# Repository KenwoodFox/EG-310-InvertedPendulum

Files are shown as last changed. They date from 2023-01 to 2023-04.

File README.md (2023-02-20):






EG-310 Inverted Pendulum
========================

This project is full of blank media! It will need filling out and cleaning before production, you have been warned!

# Welcome!

Put a welcome here!

# Getting Started

## Cloning this repo

First, clone this repo (and optionally checkout a branch)

```shell
git clone https://github.com/KenwoodFox/InvertedPendulum.git
cd InvertedPendulum
```

## Init Submodules

Some libraries and resources are included as git submodules, run the following
command to initialize them before opening the main sch

(If you get a missing library error, make sure to do this!)

```shell
git submodule update --init --recursive
```

# Where is everything?!

Look to...
```shell
├── CAD                     # CAD and design files
├── Firmware                # Software and Firmware source code
├── Hardware                # PCB And component design files
└── Media
    ├── Notes               # Notes and scratch ideas/misc resources
    ├── Letters             # Status letters, letters of request, etc
    └── Presentations       # Presentations (CDR, FDR..)
```

# I just want to edit a single file!

Start by cloning this repo down and making a new branch, offical team communication
is through discord so hop on over any time! If you're new to git check out this video: https://youtu.be/mJ-qvsxPHpY

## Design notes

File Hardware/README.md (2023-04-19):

# Hardware

All the hardware for the inverted pendulum is made with (KiCAD)[https://www.kicad.org/]!

All the automation for this project is done with (KiBot)[https://github.com/INTI-CMNB/KiBot]

## Getting Started

Always clone this repo using submodules!

```shell
git clone --recurse-submodules https://github.com/KenwoodFox/EG-310-InvertedPendulum.git
```

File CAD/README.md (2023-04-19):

# CAD

The cad is a mix of Inventor and FreeCAD.

## Directory

```
.
├── Components                                            ; FreeCAD Misc Parts
├── Cosmetic                                              ; Badges and cosmetic
├── Frame Pieces                                          ; Frame Pieces
├── Matt's CDR CAD Files (Inventor Professional Format)   ; Matt's Inventor Files
│   ├── Assemblies                                        ; Inventor Assemblies
│   │   ├── Carriage Assemblies
│   │   └── Frame Assemblies
│   ├── Components and Part Files                         ; Inventor Components and Parts
│   │   ├── Carriage Components
│   │   └── Frame Components
│   ├── Drawings                                          ; Inventor Drawings
│   │   └── Different Carriage Type Exploded Drawings
│   └── Exploded Views                                    ; Exploded Views
│       └── DIfferent Carriage Type Presentations
└── Resources                                             ; Resources stencils and templates
```

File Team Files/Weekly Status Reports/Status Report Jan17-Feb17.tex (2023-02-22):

% Formatting
\documentclass{scrartcl}
\usepackage{hyperref}
\usepackage{makeidx}
    \makeindex
\usepackage{xparse}

\usepackage{graphicx}
\graphicspath{ {.} }

\usepackage[most]{tcolorbox}
\NewDocumentCommand\newtcbtheoremautoindex{ O{} m  m m m }{%%
\newtcbtheorem[#1]{#2inner}{#3}{#4}{#5}%
\NewDocumentEnvironment { #2 } { s O{} m m }
{\IfBooleanTF{##1}
   {\begin{#2inner}[##2]{##3}{##4}}% not to index
   {\begin{#2inner}[##2, index={##3}]{##3}{##4}}% to index
} {\end{#2inner}}
% starred version (not labeled and not listed in lists of theorems):
\NewDocumentEnvironment { #2* } { O{} m }
   {\begin{#2inner*}[##1]{##2}}% (and no index as well)
   {\end{#2inner*}}
}%%

\newtcbtheoremautoindex[]{defi}{}{}{def}

% End formatting

% ====================
% Begin Status report!
% ====================

\begin{document}
\section*{EG-310 Weekly Status Report}
\begin{center}
    \begin{tabular}{ l l }
        Project Lead     & Joseph Sedutto          \\
        Date             & \today         \\
        Reporting Period & January 17 - Febuary 17
    \end{tabular}
\end{center}

\begin{defi}{Project Status Summary}{}
    \begin{tabular}{ l l r }
        Budget   & On Track & We have begun spending and qouting         \\
        Schedule & On Track & We are slightly behind schedule                     \\
        Scope    & On Track & We are within scope.
    \end{tabular}
\end{defi}

\begin{defi}{Work Completed this week}{}
    - Created inital frame and CAD \\
    - Completed inital revision of PCB \\
    - Completed PDR and presented \\
    - Reviewed PDR feedback and created inital CDR
\end{defi}

\begin{defi}{Open issues}{}
    % Check open issues https://github.com/KenwoodFox/EG-310-InvertedPendulum/issues
    No issues and \href{https://github.com/KenwoodFox/EG-310-InvertedPendulum/pulls}{four pull requests} are waiting for feedback or review.
\end{defi}

\begin{defi}{Todo for next week}{}
    % Check projects tab https://github.com/users/KenwoodFox/projects/1
    - Finalize PDP draft for submission on January 30, 2021.  \\ 
    - Convert PDP data into a simplistic slideshow format. \\
    - Create more sketches of subassemblies and identify subassemly requirements.
\end{defi}

\begin{defi}{Comments/Team Dynamics}{}
    - Everyone still seems cheerful!
\end{defi}

\pagebreak
\section{Meeting Notes}
% Include meeting notes verbatim
\lstinputlisting[breaklines=true]{../Meeting Minutes/Week29-17.md}

\pagebreak
\section{Releases Published This Week}

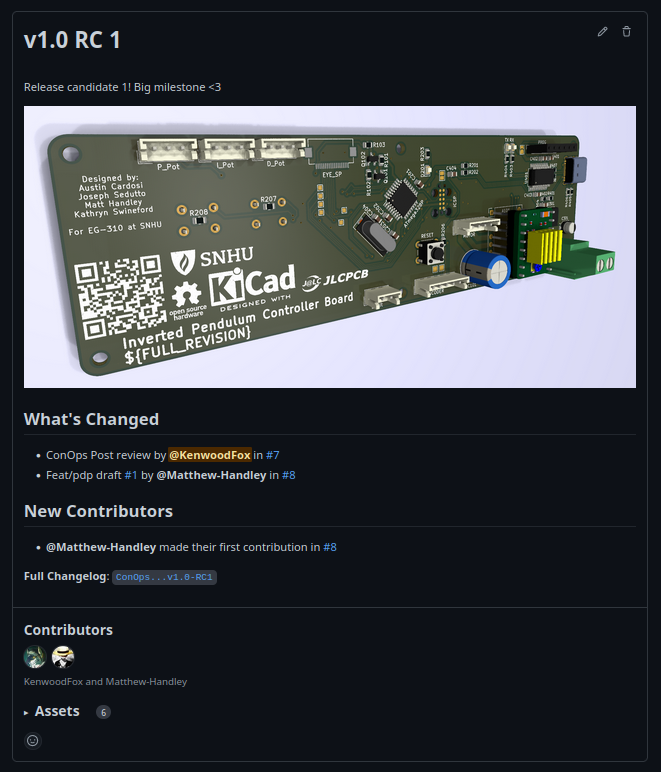
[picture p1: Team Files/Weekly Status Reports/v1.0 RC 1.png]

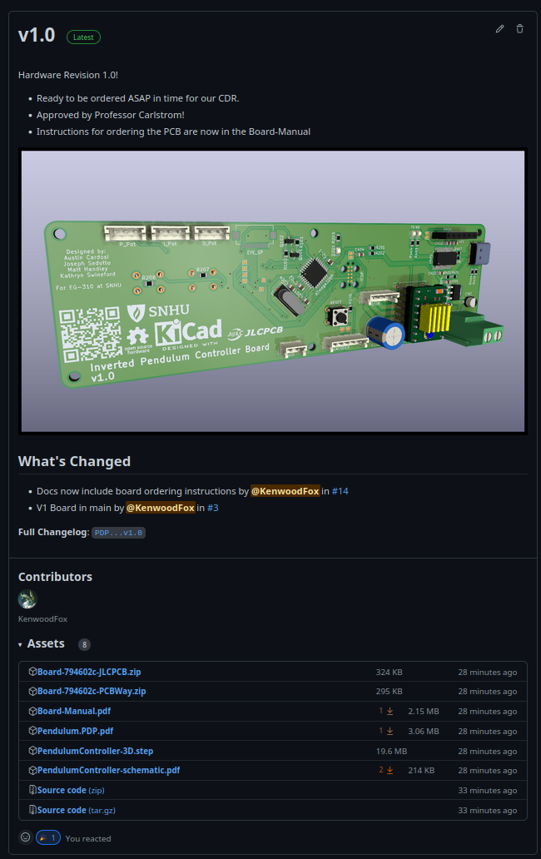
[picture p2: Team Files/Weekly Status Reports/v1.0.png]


\end{document}

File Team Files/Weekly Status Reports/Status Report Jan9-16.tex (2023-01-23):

% Formatting
\documentclass{scrartcl}
\usepackage{hyperref}
\usepackage{makeidx}
    \makeindex
\usepackage{xparse}

\usepackage[most]{tcolorbox}
\NewDocumentCommand\newtcbtheoremautoindex{ O{} m  m m m }{%%
\newtcbtheorem[#1]{#2inner}{#3}{#4}{#5}%
\NewDocumentEnvironment { #2 } { s O{} m m }
{\IfBooleanTF{##1}
   {\begin{#2inner}[##2]{##3}{##4}}% not to index
   {\begin{#2inner}[##2, index={##3}]{##3}{##4}}% to index
} {\end{#2inner}}
% starred version (not labeled and not listed in lists of theorems):
\NewDocumentEnvironment { #2* } { O{} m }
   {\begin{#2inner*}[##1]{##2}}% (and no index as well)
   {\end{#2inner*}}
}%%

\newtcbtheoremautoindex[]{defi}{}{}{def}

% End formatting

% ====================
% Begin Status report!
% ====================

\begin{document}
\section*{EG-310 Weekly Status Report}
\begin{center}
    \begin{tabular}{ l l }
        Project Lead     & Matt Handley          \\
        Date             & \today         \\
        Reporting Period & January 9 - 16
    \end{tabular}
\end{center}

\begin{defi}{Project Status Summary}{}
    \begin{tabular}{ l l r }
        Budget   & On Track & We have not spent anything yet.         \\
        Schedule & On Track & We are on schedule.                     \\
        Scope    & On Track & We are within scope. (No Feature creep)
    \end{tabular}
\end{defi}

\begin{defi}{Work Completed this week}{}
    - Created drawings for carriage and belt tensioner assembly. \\
    - Submitted ConOps Draft 1, and finalized and submitted our Project Schedule.
\end{defi}

\begin{defi}{Open issues}{}
    % Check open issues https://github.com/KenwoodFox/EG-310-InvertedPendulum/issues
    No issues and \href{https://github.com/KenwoodFox/EG-310-InvertedPendulum/pull/7}{one pull request} is waiting for feedback on ConOps.
\end{defi}

\begin{defi}{Todo for next week}{}
    % Check projects tab https://github.com/users/KenwoodFox/projects/1
    - Finalize PDP draft for submission on January 30, 2021.  \\ 
    - Convert PDP data into a simplistic slideshow format. \\
    - Create more sketches of subassemblies and identify subassemly requirements.
\end{defi}

\begin{defi}{Comments/Team Dynamics}{}
    - Sunday's meeting was canceled as there was a schedule mix-up. \\
    - Austin C. has been MIA for team meetings and has not responded through messaging.
\end{defi}

\pagebreak
\section{Meeting Notes}
% Include meeting notes verbatim
\lstinputlisting[breaklines=true]{../Meeting Minutes/Week9-16.md}

\end{document}

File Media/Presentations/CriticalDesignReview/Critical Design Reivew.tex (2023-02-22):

\documentclass[aspectratio=169]{beamer}

\setbeameroption{show notes on second screen}

\usepackage[utf8]{inputenc}
\usetheme{Madrid}
\usecolortheme{beaver}

\usepackage{graphicx}
\graphicspath{ {../Resources/} }

\title{Critical Design Review}       % Title
\author{Austin, Kathryn, Matt, Joe}                     % Team members
\institute{SNHU/CETA}                                   % Institute
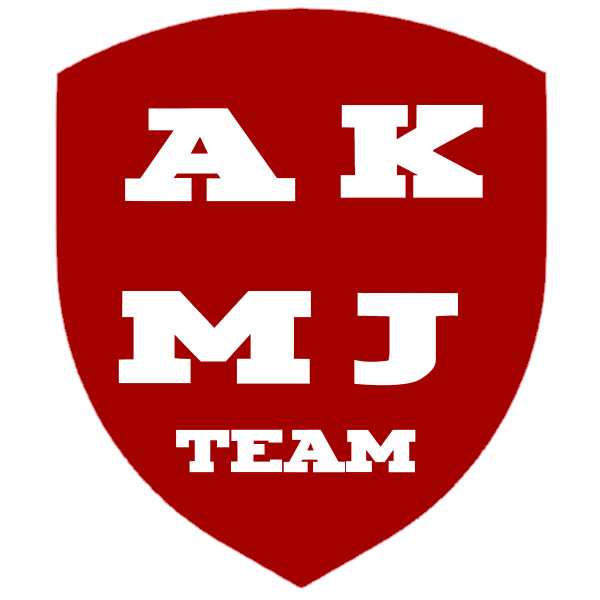
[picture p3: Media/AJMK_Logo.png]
\logo{}  % Our Logo
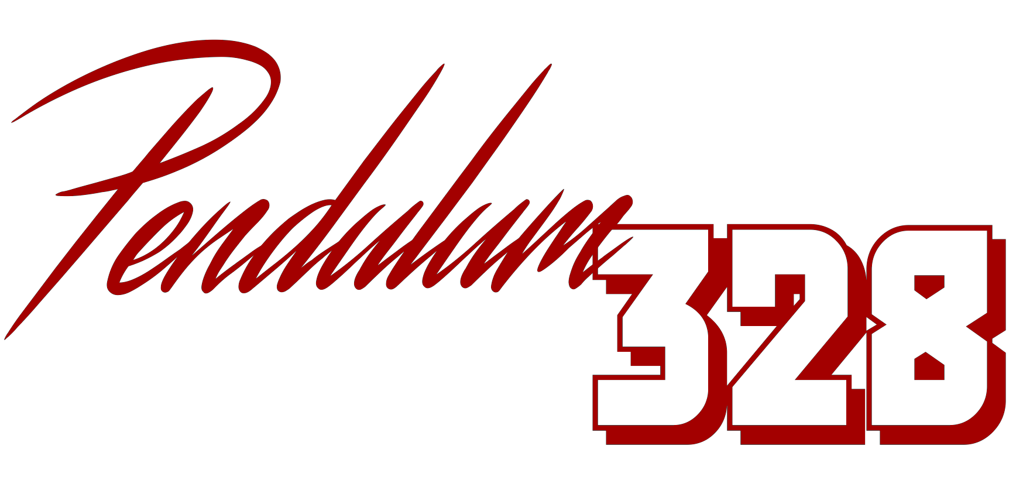
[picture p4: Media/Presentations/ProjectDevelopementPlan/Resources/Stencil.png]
\titlegraphic{} % Title graphic

\begin{document}

\frame{\titlepage} % Draw the title page
\note{Title page notes here.}

\section{Introduction}

\begin{frame}
    \frametitle{Agenda}

    \begin{columns}
    \begin{column}{0.48\textwidth}
        \setcounter{tocdepth}{1} % Prof requested we do this
        {\tableofcontents}
    \end{column}

    \begin{column}{0.48\textwidth}
        \begin{center}
            
            
        \end{center}
    \end{column}
    \end{columns}

\note{
\huge Everyone \normalsize

\begin{itemize}
 \item We'll do questions at the end
 \item Page numbers are in the bottom right, remember to note what page you'd like us to go back to!
\end{itemize}
}
\end{frame}

\begin{frame}
    \frametitle{What is PID}

    \begin{columns}
        \begin{column}{0.48\textwidth}
            \begin{block}{What is PID}
                PID (Proportional, Integral, Derivative),
                is an algorithm designed to minimize the
                \textbf{error} in a system.
            \end{block}
        \end{column}

        \begin{column}{0.48\textwidth}
            \begin{block}{Where do we see PID loops?}
                The error can be any error, as long as it can be measured.
                \begin{itemize}
                 \item Cruise Control in a car (speed of the car)
                 \item Thermostats (Temperature)
                 \item Engine governors (Torque output)
                 \item Laptop fan controller (Dissipated heat)
                 \item Dynamic CPU turbo scaling (Optimal performance)
                \end{itemize}
            \end{block}
        \end{column}
    \end{columns}

    \note{
        \huge Joe \normalsize

        A PID loop should be familer to many engineers but in short, its a method for
        minimizing the error in a system.

        The system can be any system, as long as its error can be measured, some common
        examples include
        \begin{itemize}
         \item Cruise control
         \item Thermostats
         \item Engine govoners
         \item Fan controllers
         \item And CPU Turbo scaling
        \end{itemize}
    }
\end{frame}

\begin{frame}
    \frametitle{High level Overview}

    \begin{columns}
        \begin{column}{0.48\textwidth}
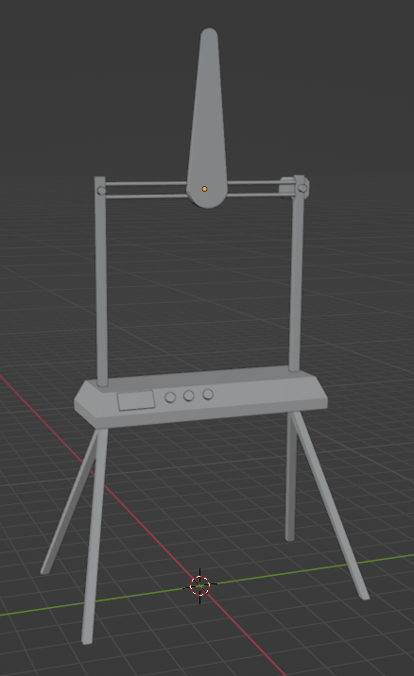
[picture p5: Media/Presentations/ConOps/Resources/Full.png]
            
        \end{column}

        \begin{column}{0.48\textwidth}
            \begin{block}{Overview}
                Develop a system that can..
                \begin{enumerate}
                 \item Design
                 \item Train
                 \item Educate
                \end{enumerate}

                On the topic of PID systems.
            \end{block}
        \end{column}
    \end{columns}

    \note{
        \huge Austin \normalsize

        We are building a PID Demonstrator, witch is a tool designed
        to train, educate and sharpen the skills required for engineers
        and operators to train PID loops. Which are a common algorithm
        that drive many modern systems.
    }
\end{frame}

\begin{frame}
    \frametitle{Block Diagram}

    \begin{columns}
        \begin{column}{0.70\textwidth}
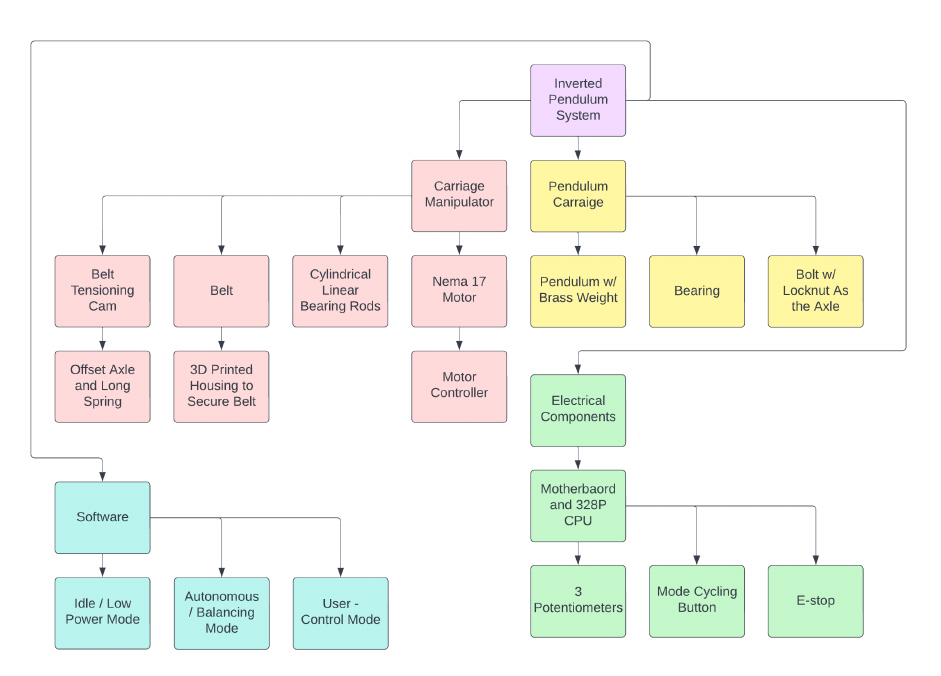
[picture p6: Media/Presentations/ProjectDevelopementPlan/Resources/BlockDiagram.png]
            
        \end{column}

        \begin{column}{0.30\textwidth}
            \begin{block}{Block Diagram}
                The block diagram details the electrical, mechanical and software components and their relationship to each other.
            \end{block}
        \end{column}
    \end{columns}

\note{
\huge Matt \normalsize

\begin{itemize}
 \item Our block diagram shows how our software, hardware and electronics may interact in a final system
\end{itemize}
}

\end{frame}

\begin{frame}
    \frametitle{ConOps Summary}

    \begin{columns}

    \begin{column}{0.34\textwidth}
        Stakeholders
        \begin{itemize}
         \item SNHU
         \item Professors
         \item Industrial Trainers
         \item Parts and manufacturers
        \end{itemize}

        Users
        \begin{itemize}
         \item Pendulum Team
         \item Educators
        \end{itemize}
    \end{column}

    \begin{column}{0.65\textwidth}
        \begin{block}{Operating Modes}
            \begin{enumerate}
            \item Off mode
            \item Idle mode
            \item Spinup mode
            \item Demo mode
            \item User PID mode
            \end{enumerate}
        \end{block}

        \begin{block}{System Description}
            \small{An inverted pendulum is a type of PID Demonstrator, where a simple PID loop
            controls and minimizes the error in a system. In this case, the error is the angle of the pendulum. A perfectly tuned PID loop will hover the pendulum}
            \textbf{perfectly still}.
        \end{block}
    \end{column}
\end{columns}

\note{
\huge Matt \normalsize

\begin{itemize}
 \item So our stakeholders include SNHU, our professors, industrial trainers and of course the people who supply parts and manufacturer our product.
 \item At the moment, we're the ones manufacturing it but in the future it could be different.
 \item Our users are us and educators who might want to use this product to teach the fundamentals of PID
 \item It has a few modes, Off, Idle, Spinup, Demo and user PID mode. The last two are where the pendulum self-balances
 \item Its almost like a game, the system is naturally unstable, the pendulum wants to fall, but a properly tuned PID loop can keep it upright!
\end{itemize}
}

\end{frame}

\begin{frame}
    \frametitle{ConOps (cont.)}

    \begin{columns}
        \begin{column}{0.48\textwidth}
            \begin{block}{Operation and Support Environment}
                \begin{itemize}
                 \item Built from COTS (common off the shelf) parts
                 \item Designed to be serviced
                 \item Constant uptime
                 \item Low power modes
                \end{itemize}
            \end{block}
        \end{column}

        \begin{column}{0.48\textwidth}
            \begin{block}{Impact considerations}
                \begin{itemize}
                 \item Requiring physical space, either for storage or use.
                 \item Being a hazard and risking misuse.
                 \item Generating pollutants and disposal.
                \end{itemize}
            \end{block}
        \end{column}
    \end{columns}

\note{
\huge Matt \normalsize

\begin{itemize}
 \item Being built from COTS parts allows us to easily replace components and design service schedules
 \item We also have plans for a low power mode and folding or removable legs to decrease electrical and physical footprint.
\end{itemize}
}

\end{frame}

\section{Software/Electrical}
\begin{frame}
    \frametitle{The Software/Electrical Subsystem}

    

    \note{
        \huge Joe \normalsize

        In our system the software and hardware are very closely
        linked.

        We have several features such as the E-Stop that
        rely heavily on an integration between embedded code
        and physical electrical hardware interlocks.
    }
\end{frame}

\begin{frame}
    \frametitle{The Software/Electrical Subsystem (cont.)}

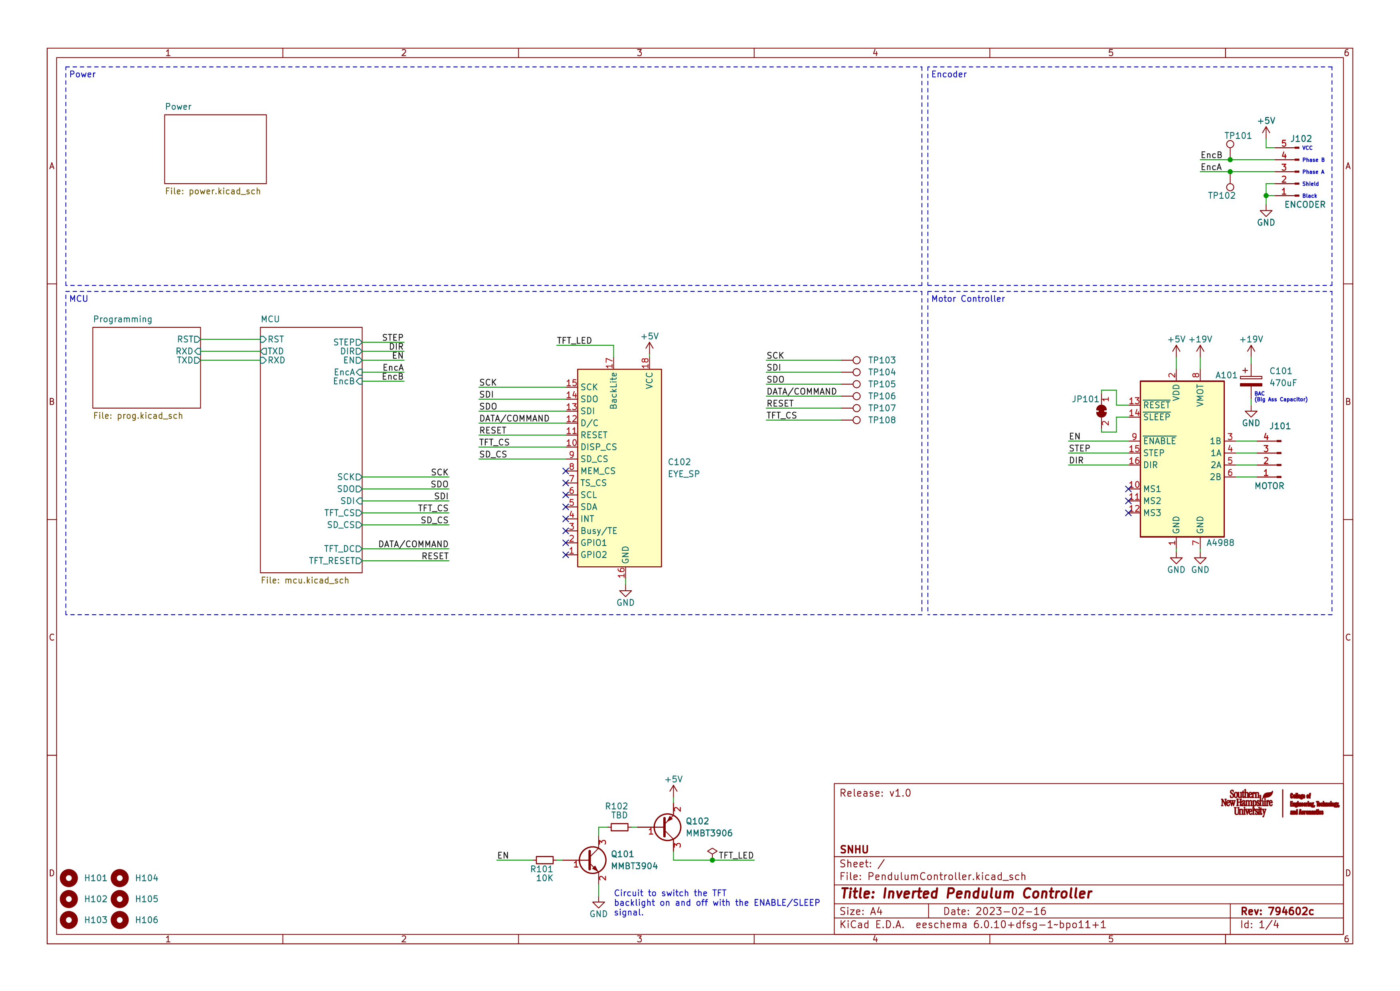
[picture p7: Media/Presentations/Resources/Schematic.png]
    

    \note{
        \huge Joe \normalsize

        We've designed the general circuitry to take advantage of every
        safety feature the 328p offers such as:
        \begin{enumerate}
         \item A hardware watchdog
         \item Integrated current monitoring
         \item A standby shutdown
         \item And an integrated clock
        \end{enumerate}

    }
\end{frame}

\begin{frame}
    \frametitle{Summary of Trade Studies}

    \begin{columns}
        \begin{column}{0.70\textwidth}
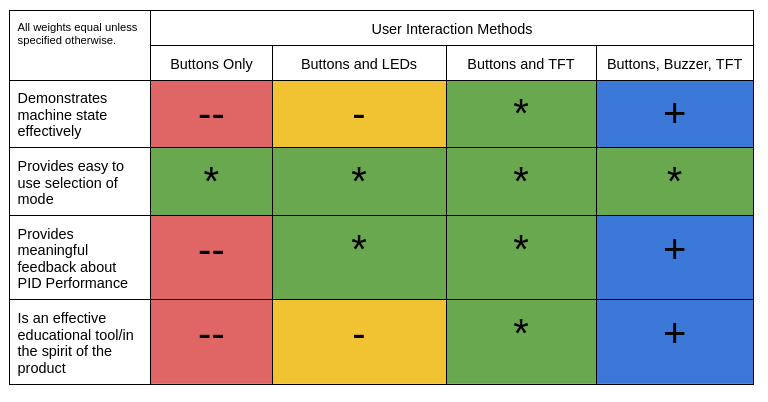
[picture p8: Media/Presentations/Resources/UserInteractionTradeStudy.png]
            
        \end{column}

        \begin{column}{0.28\textwidth}
            \begin{block}{User Interactions}
                The way the user interacts with our system is an important
                part of our design. If the system does not meaningfully
                interact with the operator, then it does not perform
                to our requirements.
            \end{block}
        \end{column}
    \end{columns}

    \note{
        \huge Joe \normalsize

        The way that the user interacts with the system is very important to our project.
        We want a product that will effectively communicate how and why a PID loop
        works.

        Our chart places the TFT plus buzzer, plus buttons as the best for our requirements.
    }
\end{frame}

\begin{frame}
    \frametitle{Summary of Trade Studies (cont.)}

    \begin{columns}
        \begin{column}{0.70\textwidth}
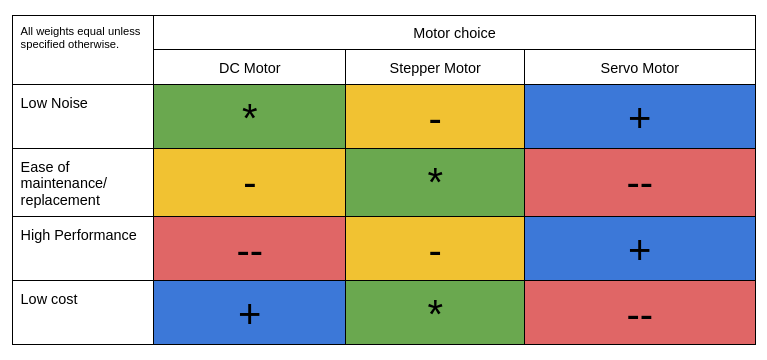
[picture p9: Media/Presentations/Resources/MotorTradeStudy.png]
            
        \end{column}

        \begin{column}{0.28\textwidth}
            \begin{block}{Motors}
                We use our requirements to balance weight, sound
                cost and performance.
            \end{block}
        \end{column}
    \end{columns}

    \note{
        \huge Joe \normalsize

        The motor we choose will affect performance as well as noise and cost. We
        decided to go with a simple stepper motor.
    }
\end{frame}

\begin{frame}
    \frametitle{Software Flowchart}

    \begin{columns}
        \begin{column}{0.72\textwidth}
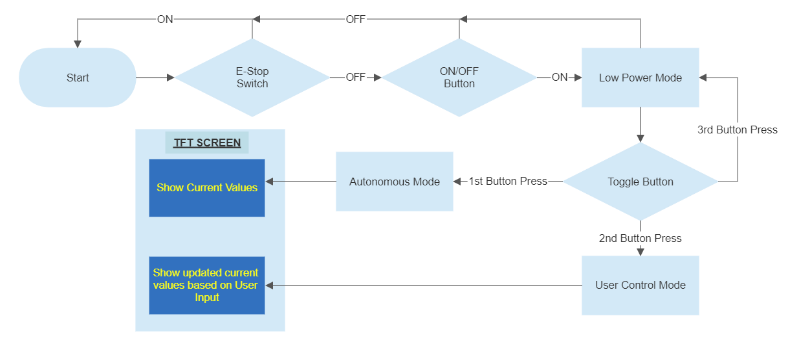
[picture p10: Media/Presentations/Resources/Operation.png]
            
        \end{column}

        \begin{column}{0.28\textwidth}
            \begin{block}{Software Flowchart}
                The software flowchart is an overview of all the software functions of our
                proposed product.
            \end{block}
        \end{column}
    \end{columns}

\note{
\huge Austin \normalsize

\begin{itemize}
 \item Our software flowchart details how the PID control scheme will be interactable by the users
\end{itemize}
}

\end{frame}

\begin{frame}
    \frametitle{Verification Plan (Electrical/Software)}

    \begin{columns}
        \begin{column}{0.58\textwidth}
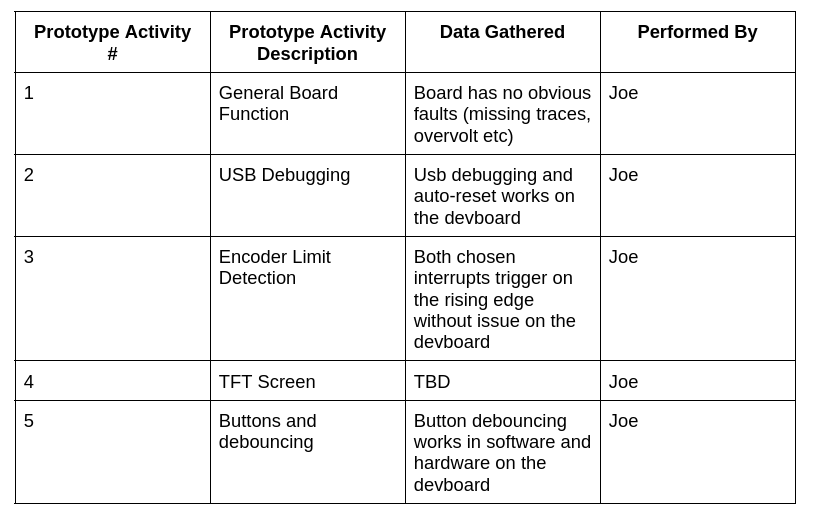
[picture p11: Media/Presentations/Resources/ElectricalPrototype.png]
            
        \end{column}

        \begin{column}{0.40\textwidth}
            \begin{block}{Block Diagram}
                \tiny{
                    Mainboard requires several important features:
                    \begin{enumerate}
                        \item E-Stop
                        \item Button Inputs
                        \item Potentiometers
                        \item Encoder
                        \item Motor output
                        \item Limit Switch
                        \item TFT Screen
                    \end{enumerate}

                    The prototype board implements all these features as well as...
                    \begin{enumerate}
                        \item USB Programming/debugging
                        \item Status lights
                        \item Mode and start select buttons
                        \item Onboard VRM
                    \end{enumerate}
                }
            \end{block}
        \end{column}
    \end{columns}

    \note{
        \huge Austin \normalsize

        The electrical components must adheere to the standards we set
        and must pass our tests

        The most important tests are that the board \textbf{Generally Functions}
        and that we can \textbf{Program and Debug} it without an external
        programmer.
    }
\end{frame}

\section{Mechanical System}
\begin{frame}
    \frametitle{The Mechanical Subsystem}

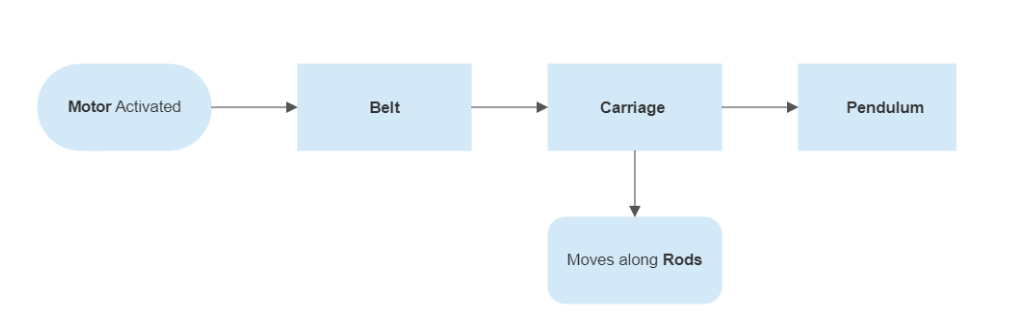
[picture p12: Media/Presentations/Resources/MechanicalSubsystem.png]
    

    \note{
        \huge Austin \normalsize

        We love you austin!
    }
\end{frame}

\begin{frame}
    \frametitle{System Design}

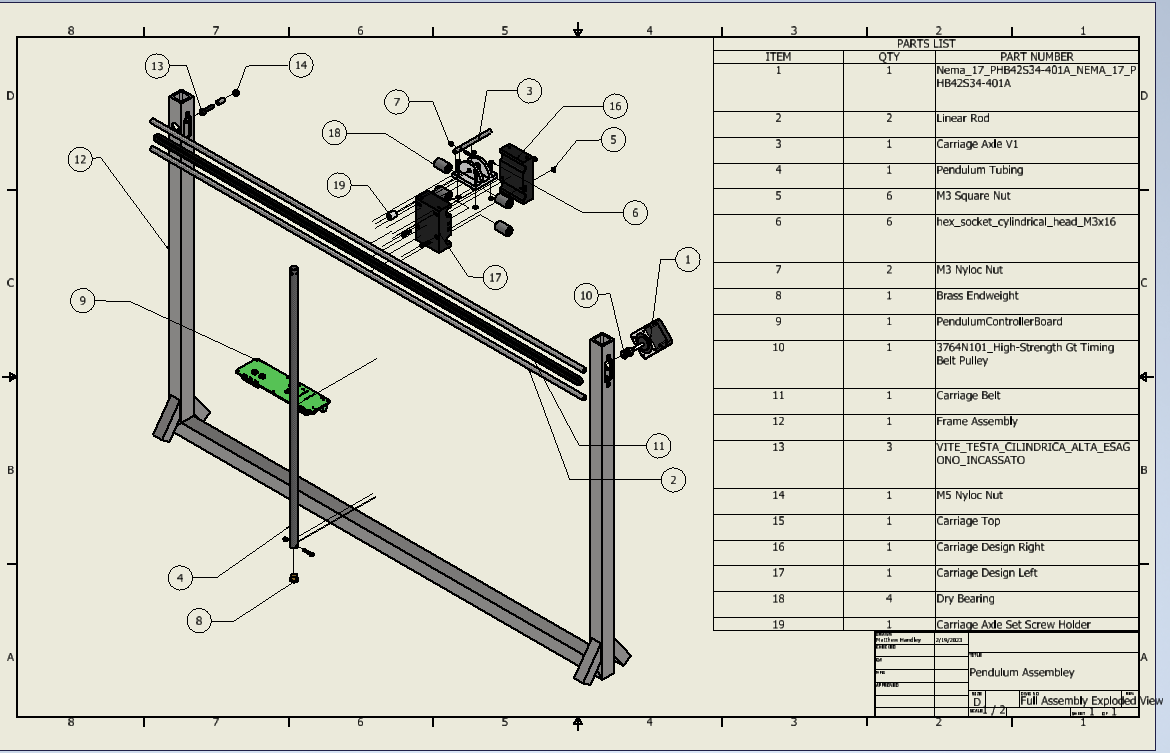
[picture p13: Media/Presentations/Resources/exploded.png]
    

    \note{
        \huge Matt \normalsize

        Note that the tubing contains all cutouts and motor mounts, eliminating
        the need for expensive dedicated brackets and fixtures.
    }
\end{frame}

\begin{frame}
    \frametitle{Summary of Trade Studies}

    \begin{columns}
        \begin{column}{0.28\textwidth}
            \begin{block}{Bearings}
                Choosing bearings that meet our minimum requirements
                helps us to design a system that meets the needs we
                expect to solve.
            \end{block}
        \end{column}

        \begin{column}{0.70\textwidth}
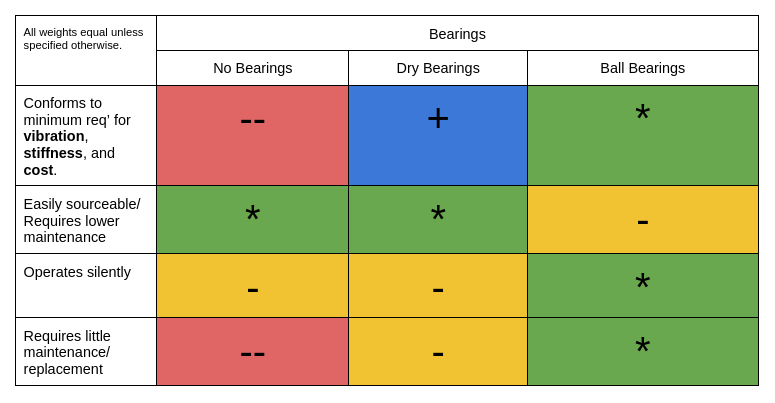
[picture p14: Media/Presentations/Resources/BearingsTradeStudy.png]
            
        \end{column}
    \end{columns}

    \note{
        \huge Matt \normalsize

        To meet the minimum Requirements we've outlined our bearings must be
        \begin{itemize}
         \item Inexpensive
         \item Quiet
         \item and must support the weight of the carriage
        \end{itemize}
    }
\end{frame}

\begin{frame}
    \frametitle{Summary of Trade Studies (cont.)}

    \begin{columns}
        \begin{column}{0.28\textwidth}
            \begin{block}{Material Choice}
                Each material has pros and cons.
            \end{block}
        \end{column}

        \begin{column}{0.70\textwidth}
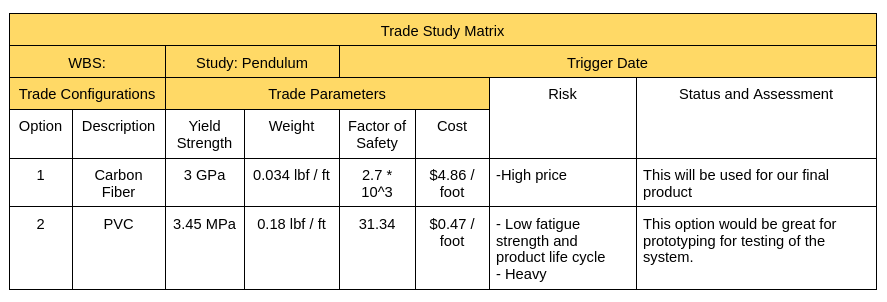
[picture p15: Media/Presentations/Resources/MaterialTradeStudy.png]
            
        \end{column}
    \end{columns}

    \note{
        \huge Matt \normalsize

        The material choice affects cost as well as weight, noise and performance.
    }
\end{frame}

\begin{frame}
    \frametitle{Summary of Trade Studies (cont.)}

    \begin{columns}
        \begin{column}{0.70\textwidth}
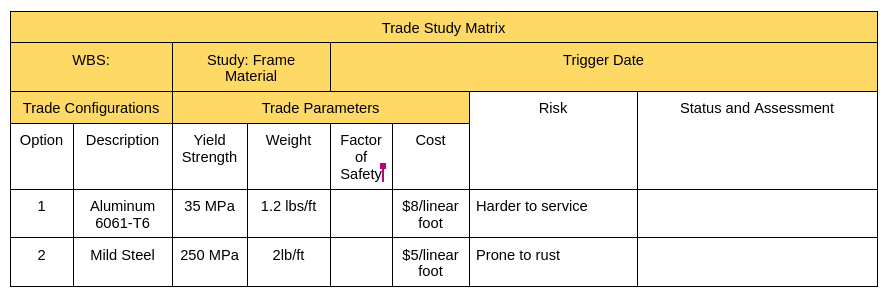
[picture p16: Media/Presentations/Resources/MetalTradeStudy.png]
            
        \end{column}

        \begin{column}{0.28\textwidth}
            \begin{block}{Metal}
                The metal we select affects safety and cost.
            \end{block}
        \end{column}
    \end{columns}

    \note{
        \huge Matt \normalsize

        Idk, wing it man
    }
\end{frame}

\begin{frame}
    \frametitle{Summary of Trade Studies (cont.)}

    \begin{columns}
        \begin{column}{0.28\textwidth}
            \begin{block}{NEMA Motor Choice}
                The specific type of stepper motor impacts strngth and idle power.
            \end{block}
        \end{column}

        \begin{column}{0.70\textwidth}
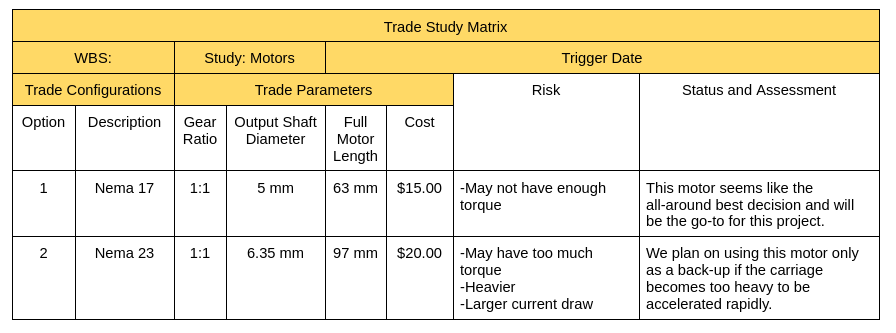
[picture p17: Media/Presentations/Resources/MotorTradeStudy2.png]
            
        \end{column}
    \end{columns}

    \note{
        \huge Matt \normalsize
    }
\end{frame}

\begin{frame}
    \frametitle{Operations}

    \begin{columns}
        \begin{column}{0.30\textwidth}
            \begin{block}{Operations}
                The Operations diagram details the physical and general controls.
            \end{block}
        \end{column}

        \begin{column}{0.70\textwidth}
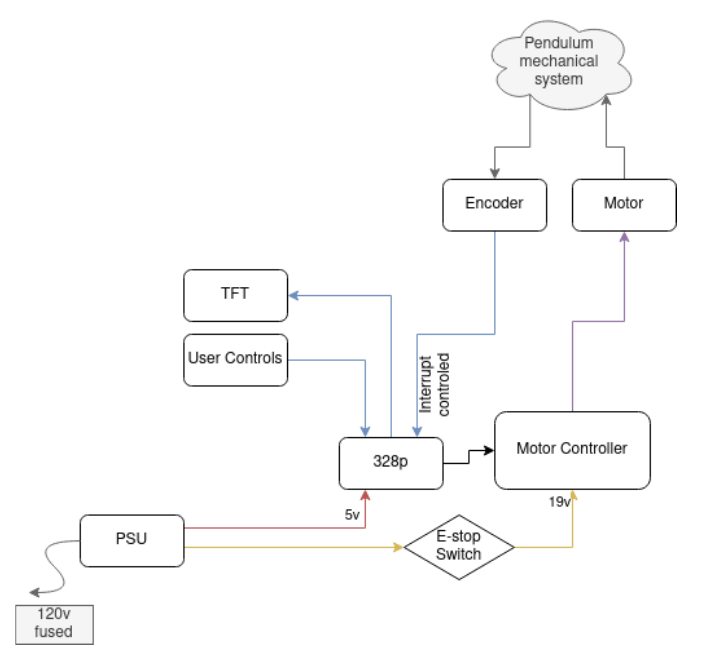
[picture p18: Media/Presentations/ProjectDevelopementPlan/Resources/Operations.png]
            
        \end{column}
    \end{columns}

\note{
\huge Joe \normalsize

\begin{itemize}
 \item The operations chart details our physical and general controls like the tft screen
 \item the buttons
 \item the motor controller and encoders
\end{itemize}
}

\end{frame}

\begin{frame}
    \frametitle{Verification Plan (Mechanical)}

    \begin{columns}
        \begin{column}{0.40\textwidth}
            \begin{block}{Block Diagram}
                \tiny{
                    Each bearing is tested and evaluated with the above chart, with specific attention to:
                    \begin{enumerate}
                        \item Cost of bearing (4 needed for every pendulum)
                        \item Noise (Minimize sliding grinding noises)
                        \item Performance (How well does it slide and protect the carriage shafts)
                        \item Longevity (How long does it last without service or lube?)
                    \end{enumerate}
                }
            \end{block}
        \end{column}

        \begin{column}{0.58\textwidth}
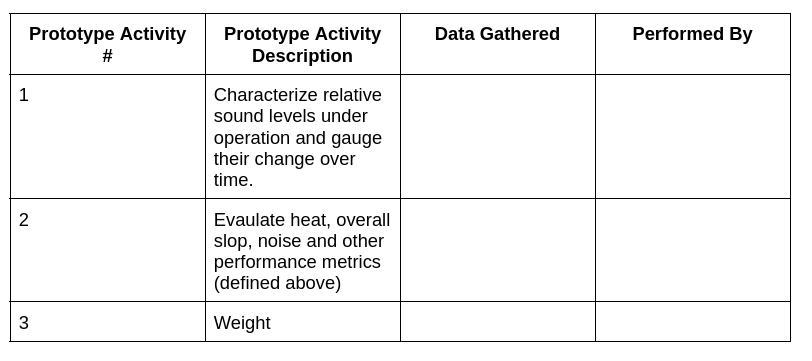
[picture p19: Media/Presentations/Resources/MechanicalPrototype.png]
            
        \end{column}
    \end{columns}

    \note{
        \huge Matt \normalsize
    }
\end{frame}

\section{Requirements}
\begin{frame}
    \frametitle{Functional Requirements}

    \begin{columns}
        \begin{column}{0.70\textwidth}
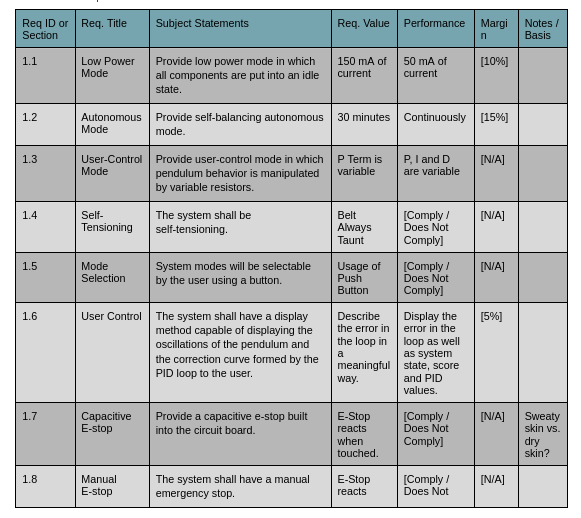
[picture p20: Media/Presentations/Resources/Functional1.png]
            
        \end{column}

        \begin{column}{0.28\textwidth}
            \begin{block}{Functional Requirements}
                Many of our functional requirements include features such as
                a different modes and mode slections. As well as limits on
                weight, power draw and assembly time.
            \end{block}
        \end{column}
    \end{columns}

    \note{
        \huge Matt \normalsize
    }
\end{frame}

\begin{frame}
    \frametitle{Functional Requirements (cont.)}

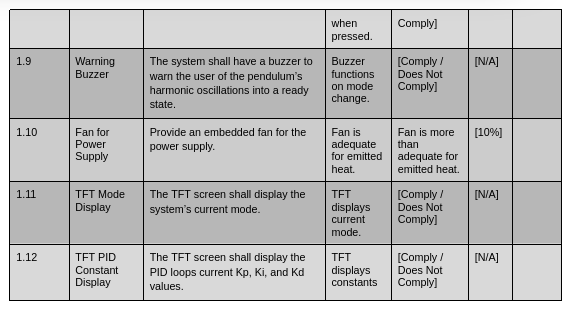
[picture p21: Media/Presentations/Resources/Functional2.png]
    

    \note{
        \huge Joe \normalsize
    }
\end{frame}

\begin{frame}
    \frametitle{Performance Requirements}

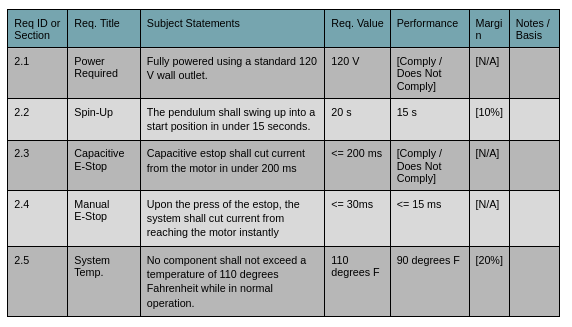
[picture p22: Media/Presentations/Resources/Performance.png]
    

    \note{
        \huge Austin \normalsize

        We'll need to meed specific functional requirements like displaying
        the mode and keeping the power supply cool.
    }
\end{frame}

\begin{frame}
    \frametitle{Interface and Design Requirements}

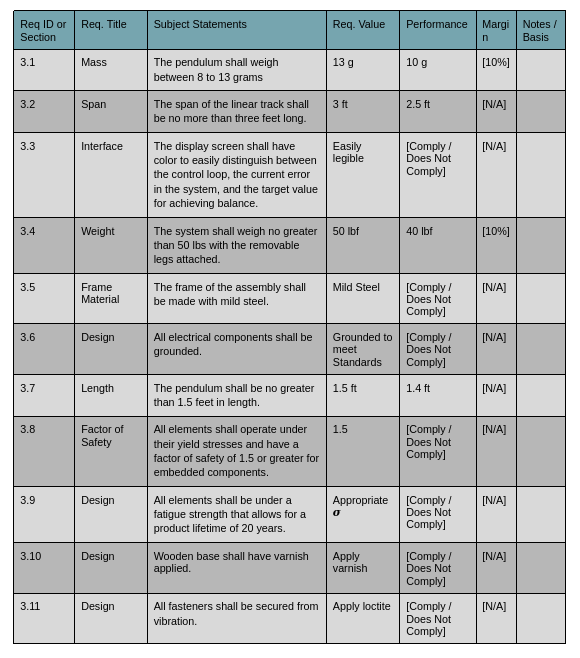
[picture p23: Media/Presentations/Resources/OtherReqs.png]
    

    \note{
        \huge Joe \normalsize

        We'll need to inteface to existing infrastructure such as
        120v AC and have standardized e-stop technology
    }
\end{frame}

\section{Design}
\begin{frame}
    \frametitle{Bill Of Materials}

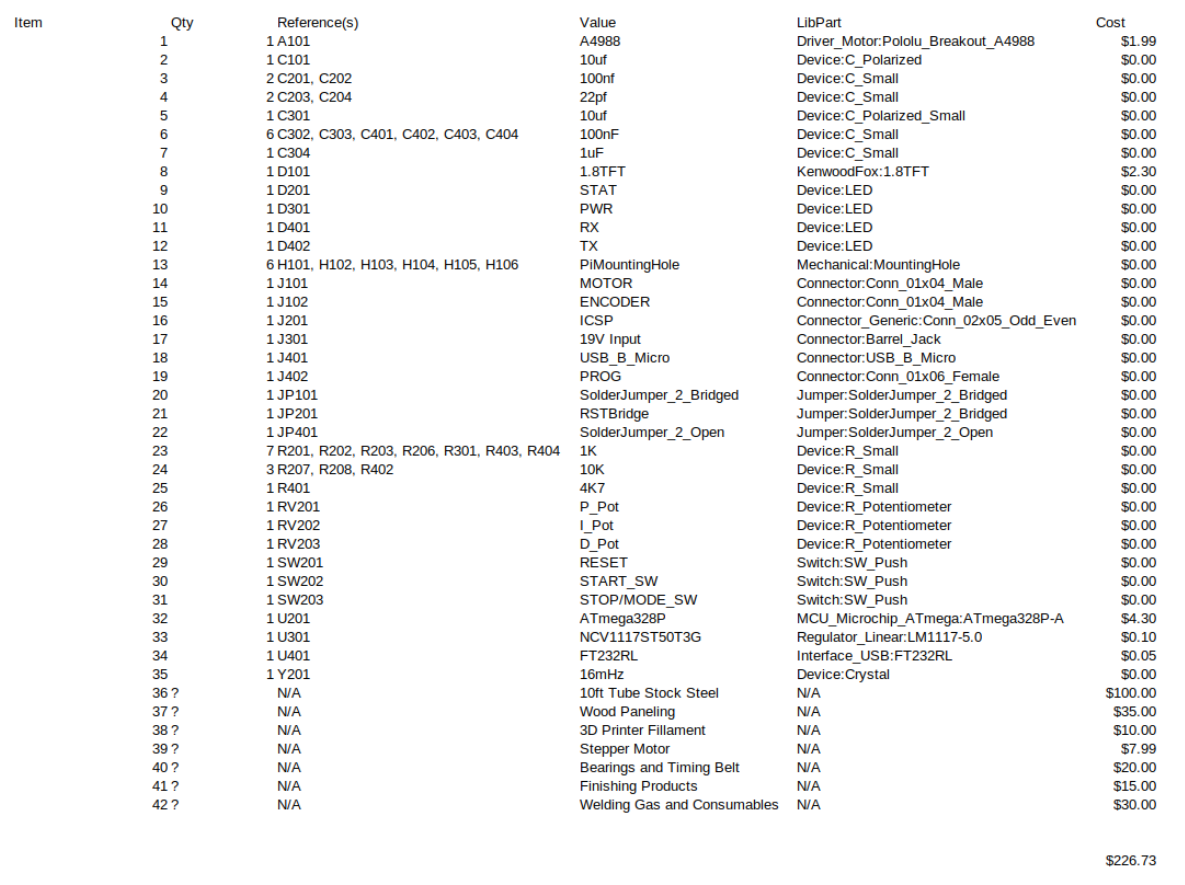
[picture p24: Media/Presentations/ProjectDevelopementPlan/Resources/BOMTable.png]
    

    \note{
        \huge Matt \normalsize

        Our bill of materials is very long but everything is here even down
        to the smallest individual components.
    }
\end{frame}

\begin{frame}
    \frametitle{Ordering Status}

    \begin{block}{Bearings}
        Dry bearings have arrived, ball bearings still in mail.
    \end{block}

    \begin{block}{PCB}
        PCB Confirmed Ordered.
    \end{block}

    \begin{block}{Steel}
        We're in the process of sourcing steel.
    \end{block}

    \begin{block}{3D/plastic/COTS}
        Material stock for welding, 3D printing and machining are ready to go.
    \end{block}

    \note{
        \huge Matt \normalsize
    }
\end{frame}

\begin{frame}
    \frametitle{Impact Considerations}

    \begin{enumerate}
        \item Being a hazard and risking misuse.
        \item Requiring physical space, either for storage or use.
        \item The system will generate waste at the end of its life cycle. The goal is to minimize this waste through the use of recyclable materials
    \end{enumerate}

    \note{
        \huge Austin \normalsize
    }
\end{frame}

\section{Calibration and Maintenance}
\begin{frame}
    \frametitle{Calibration and Maintenance}

        \begin{itemize}
            \item Self test and Auto Calibration
            \item Use of hardware limits
            \item Torque specs for all fasteners
            \item Published maintenance schedule in docs.
        \end{itemize}

    \note{
        \huge Austin \normalsize

        \begin{enumerate}
        \item The system shall perform a self-test on start-up. Due to the pendulum hanging towards the center of the earth due to gravity, the encoder on the pendulum will be zeroed using the position.
        \item The motor shall move towards a limit switch at a set slow speed until it triggers one of the two limit switches on either side of the linear rails, upon triggering one, the carriage will then move a set amount of motor steps to the middle of the span of the linear rails.
        \item All fasteners shall have their tightness ensured before operation, and any renewal of lubrical for the pendulum shall be performed.
        \item A maintenance and component replacement manual shall be created in order to easily explain how to replace the COTS (common of the shelf) parts such as the precision belt or the motor internals.
    \end{enumerate}
    }
\end{frame}

\begin{frame}
    \frametitle{Safety}

    \begin{itemize}
     \item Electrical
        \begin{itemize}
         \item E-Touch - Capacitive sensor that detects when a user has provided a static charge or short circuit and will automatically turn off the power
        \end{itemize}

    \item Software
        \begin{itemize}
         \item Limits -  Designed to restrict the upper bounds of the provided commands and to make sure the acceleration and velocities don't exceed a maximum.
        \end{itemize}

    \item Mechanical
        \begin{itemize}
            \item Emergency Stop - When pressed ON all electronics will have receive NO electric flow
            \item Protective Shield - Shield designed to protect operators from pinch points created by the movement of the carriage along the rods.
            \item Buzzer - Designed to warn the operator when the system is in autonomous “swing up” mode using harmonic oscillations
            \item Power light - The system will have an LED to indicate when it is receiving power
            \item TFT Screen - The TFT screen will display what mode the system is currently running so the operator is aware.
        \end{itemize}
    \end{itemize}

    \note{
        \huge Safety \normalsize

        Most important features are sheilding

        capactive estop

        grounding

        access to cleaning to remove dust and prevent overheating
    }
\end{frame}

\begin{frame}
    \frametitle{Phase D}

    \begin{enumerate}
        \item All drawings and assemblies are on the latest revision and meet all specifications
        \item All required parts will be ordered through Carlstrom / Joe Donovan this week (2/22/2023)
        \item Manufacturing of the frame will begin as soon as the steel is delivered, and prototyping of parts will begin once all remaining parts are delivered.
        \item Drawings and assemblies will be finalized this weekend (2/25/2023) for machining to begin.
    \end{enumerate}

    \note{
        \huge Joe \normalsize
    }
\end{frame}

\begin{frame}
    \frametitle{End}

    \begin{block}{}
        \begin{center}
            \Huge Questions and Comments?
        \end{center}
    \end{block}

    \begin{center}
        Find the source code for this document, and the rest of our designs, firmware, hardware
        and notes on GitHub!

        
    \end{center}

\note{
\begin{itemize}
 \item So please if you have any questions we would love to hear them.
 \item All of our software, CAD, hardware and design docs are licensed under
 \item \huge The MIT Open Source License \normalsize and available via git.
 \item If you have a specific slide in mind we can go back to it!
\end{itemize}
}
\end{frame}

\section{Backup Slides}
\begin{frame}
    \frametitle{Code}

    \begin{columns}
        \begin{column}{0.58\textwidth}
            
        \end{column}

        \begin{column}{0.38\textwidth}
            \begin{block}{Our Documentation}
                Find our docs online, built from the very code and CAD that
                makes our project, conforming closely to industry standards
                for industrial automation.
            \end{block}
        \end{column}
    \end{columns}
\end{frame}

\begin{frame}
    \frametitle{Online Colaboration}

    

    We use discord and github to faccilatate automatic CAD, Code, and automatic
    CI\/CD as well as..

    \begin{enumerate}
     \item Unit testing
     \item Doc generation
     \item Automated test\/deploy
     \item And project management
    \end{enumerate}
\end{frame}

\begin{frame}
    \frametitle{Carriage}

    
\end{frame}

\begin{frame}
    \frametitle{Carriage (cont.)}

    
\end{frame}

\begin{frame}
    \frametitle{End Section}

    
\end{frame}

\begin{frame}
    \frametitle{Bezel}

    
\end{frame}

\begin{frame}
    \frametitle{Carriage Render}

    
\end{frame}

\begin{frame}
    \frametitle{Calculations}

    

    Octave math model.
\end{frame}

\begin{frame}
    \frametitle{Calculations (cont.)}

    

    Hand math model.
\end{frame}

\begin{frame}
    \frametitle{Code}

    \begin{columns}
        \begin{column}{0.48\textwidth}
            
        \end{column}

        \begin{column}{0.48\textwidth}
            
        \end{column}
    \end{columns}
\end{frame}

\begin{frame}
    \frametitle{References}

    
\end{frame}

\end{document}

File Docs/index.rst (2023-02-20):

Pendulum328 Docs
================

.. toctree::
   :maxdepth: 3
   :glob:

   introduction/getting-started
   service/service
   service/assembly

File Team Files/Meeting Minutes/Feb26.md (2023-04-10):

 # Online meeting 2/26/2023

---
Attended: Joe Matt
Start Time: 5:00 PM
End Time: 5:05 PM
---

Meeting was super quick, knocked out the last of the material request form

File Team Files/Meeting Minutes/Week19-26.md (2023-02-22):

# Online meeting 2/19/2023

---
Attended: Kat, Austin, Joe, Matt
Start Time: 5:00 PM
End Time: 7:10 PM
---

worked on https://github.com/KenwoodFox/EG-310-InvertedPendulum/pull/11

Things left: Safety Slide, Calibration and Maintenance, and Impact Considerations

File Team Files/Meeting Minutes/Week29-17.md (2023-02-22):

# Online meeting 1/29/2023

---
Attended: Kat, Austin, Joe, Matt
Start Time: 5:00 PM
End Time: 6:15 PM
---

Goals:

 - Review PDP
 - Put together some inital changes
 - Upload system requirements

Completed:

 - Implemented professor suggestions
 - Upload system requirements

# In person meeting 1/30/2023

---
Attended: Joe, Matt
Start Time: 3:30 PM
End Time: 5:00 PM
---

Yay we got the pdp basically done :3 its very good, plan to get it reviewed!

# Online Meeting 2/12/2023

---
Attended: Matt, Kat, Austin and Joe arrived Late
Start Time: 3 PM
End Time: 5:00 PM
---

## today's agenda
 - send bearing links to Carlstrom
 - send pcb off

Sent off email to carlstrom containing
 - Bearings
 - PCB
 - Steel request

Got a lot done on the **CDR** google slides.

Everyone did good. Everything in purple on the CDR is left to be completed.

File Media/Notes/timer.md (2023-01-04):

# Ideas

```
[3:06 PM]KW1FOX: i know the steps are not fine, it will step and stop every time at a very fast level, but a nice smooth modulation of the steps would make me happy :3
[3:07 PM]Kaede: well, learn about fractional division in context of frequency dividers
[3:08 PM]Kaede: such algorithm even flew as Bell202 modulator
[3:08 PM]KW1FOX: Ive actually used bell202 lol haha~ I could do that for sure but, idk, still seems clunky, would it actually be inappropriate to set one of the HW timers almost every cycle?
[3:09 PM]KW1FOX: I see what ur saying tho i can just choose not to execute a step if im dividing the "fundamental" timer frequency
[3:10 PM]Kaede: you don't need to change timer division ratio on every timer overflow
[3:10 PM]Kaede: but then you need to clock second timer from output of first
[3:10 PM]Kaede: see old PLL loops with prescaler
```

# Possibly this idea?

Slow speed        |....|....|....|....|....|....|
Fast speed        |..|..|..|..|..|..|..|..|..|..|
Very fast speed   |.|.|.|.|.|.|.|.|.|.|.|.|.|.|.|

Timer             |||||||||||||||||||||||||||||||

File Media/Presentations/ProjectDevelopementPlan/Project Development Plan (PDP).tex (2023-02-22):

\documentclass[aspectratio=169]{beamer}

\setbeameroption{show notes on second screen}

\usepackage[utf8]{inputenc}
\usetheme{Madrid}
\usecolortheme{beaver}

\usepackage{graphicx}
\graphicspath{ {../Resources/} }

\title{Project Development Plan}       % Title
\author{Austin, Joe, Matt, Kathryn}                     % Team members
\institute{SNHU/CETA}                                   % Institute
\logo{}  % Our Logo
\titlegraphic{} % Title graphic

\begin{document}

\frame{\titlepage} % Draw the title page
\note{Hello and thank you for listening, We're team \huge{AKMJ} \normalsize and we're very
excited to present the PDP for our chosen product, the pendulum 328}

\section{Introduction}
\begin{frame}
    \frametitle{Problem Statement}

    \begin{columns}

    \begin{column}{0.4\textwidth}
        
    \end{column}

    \begin{column}{0.58\textwidth}
        \begin{block}{Our Goal}
        The goal is to make a PID Demonstrator that teaches the operator how to use a PID loop.
        The operator will have control to adjust each individual variable and see how each effects a
        vertical standing pendulum.
    \end{block}
    \end{column}
\end{columns}

\note{
\huge Kat \normalsize

Our goal
\begin{itemize}
 \item Make a PID Demonstrator that teaches the operator how to use a pid loop
 \item control individual variables
 \item balance the pendulum with PID
\end{itemize}
}

\end{frame}

\begin{frame}
    \frametitle{Agenda}

    \begin{columns}
    \begin{column}{0.48\textwidth}
        \setcounter{tocdepth}{1} % Prof requested we do this
        {\tableofcontents}
    \end{column}

    \begin{column}{0.48\textwidth}
        \begin{center}
            
            
        \end{center}
    \end{column}
    \end{columns}

\note{
\huge Everyone \normalsize

\begin{itemize}
 \item We'll do questions at the end
 \item Page numbers are in the bottom right, remember to note what page you'd like us to go back to!
\end{itemize}
}

\end{frame}

\section{Research}
\begin{frame}
    \frametitle{Research}

    There are a few different approaches to the PID demonstrator system.

    \begin{columns}

    \begin{column}{0.48\textwidth}
        \begin{block}{Rotary Inverted Pendulum}
             
        \end{block}
        Spins around an axis to produce its motion.
    \end{column}

    \begin{column}{0.48\textwidth}
        \begin{block}{Reaction Wheel Pendulum}
                
        \end{block}
        Uses a reaction wheel to develop a torque against falling over.
    \end{column}
\end{columns}

\note{
\huge Kat and Austin \normalsize

\begin{itemize}
 \item We performed research on other types of pid demonstrator
 \item The rotary inverted pendulum rotates around to create the torque required to balance
 \item A reaction wheel pendulum works like a spacecraft and manufactures a countertorque on the top instead of the bottom
\end{itemize}
}

\end{frame}

\section{ConOps}
\begin{frame}
    \frametitle{ConOps}

    \begin{columns}

    \begin{column}{0.34\textwidth}
        Stakeholders
        \begin{itemize}
         \item SNHU
         \item Professors
         \item Industrial Trainers
         \item Parts and manufacturers
        \end{itemize}

        Users
        \begin{itemize}
         \item Pendulum Team
         \item Educators
        \end{itemize}
    \end{column}

    \begin{column}{0.65\textwidth}
        \begin{block}{Operating Modes}
            \begin{enumerate}
            \item Off mode
            \item Idle mode
            \item Spinup mode
            \item Demo mode
            \item User PID mode
            \end{enumerate}
        \end{block}

        \begin{block}{System Description}
            \small{An inverted pendulum is a type of PID Demonstrator, where a simple PID loop
            controls and minimizes the error in a system, in this case, the error is the angle of the pendulum. A perfectly tuned PID loop will hover the pendulum.}
            \textbf{Perfectly Still}.
        \end{block}
    \end{column}
\end{columns}

\note{
\huge Matt \normalsize

\begin{itemize}
 \item So our stakeholders include SNHU, our professors, industrial trainers and of course the people who supply parts and manfucacture our product.
 \item At the moment, we're the ones manufacturing it but in the future it could be different.
 \item Our users are us and educators who might want to use this product to teach the fundamnetals of PID
 \item It has a few modes, Off, Idle, Spinup, Demo and user PID mode. The last two are where the pendulum self-balances
 \item Its almost like a game, the system is naturally unstable, the pendulum wants to fall, but a properly tuned PID loop can keep it upright!
\end{itemize}
}

\end{frame}

\begin{frame}
    \frametitle{ConOps (cont.)}

    \begin{columns}
        \begin{column}{0.48\textwidth}
            \begin{block}{Operation and Support Environment}
                \begin{itemize}
                 \item Built from COTS (common off the shelf) parts
                 \item Designed to be serviced
                 \item Constant Uptime
                 \item Low power modes
                \end{itemize}
            \end{block}
        \end{column}

        \begin{column}{0.48\textwidth}
            \begin{block}{Impact considerations}
                \begin{itemize}
                 \item Requiring physical space, either for storage or use.
                 \item Being a hazard and risking misuse.
                 \item Generating pollutants and disposal.
                \end{itemize}
            \end{block}
        \end{column}
    \end{columns}

\note{
\huge Matt \normalsize

\begin{itemize}
 \item Being built from COTS parts allows us to easily replace components and design service schedules
 \item We also have plans for a low power mode and folding or removable legs to decrease electrical and physical footprint.
\end{itemize}
}

\end{frame}

\section{Requirements}
\subsection{System Requirements}
\begin{frame}
    \frametitle{System Requirements}

    \begin{columns}
        \begin{column}{0.48\textwidth}
            \begin{block}{System Requirements}
                
            \end{block}
        \end{column}

        \begin{column}{0.48\textwidth}
            The functional requirements detail what will make our system, \textbf{our system}. Features
            that are required for us to actually \textbf{solve the problem} we want to solve.
            The most important features include having a \textbf{good user interface mode}, and safety
            systems like an \textbf{emergency stop and guards}.
        \end{column}
    \end{columns}

\note{
\huge Joe \normalsize

\begin{itemize}
 \item Our requirements are the minimums we feel that we need to hit to make our system complete the task it was designed to do
 \item Our most critical system requirements are to have a good user interface and to have saftey sytems like the emergency stop and gaurds.
\end{itemize}
}

\end{frame}

\subsection{Performance Requirements}
\begin{frame}
    \frametitle{Performance Requirements}

    \begin{columns}
        \begin{column}{0.48\textwidth}
            Performance Requirements decide critical performance targets, ie, it should be so
            fast or so quiet or so efficient. The most important in our performance requirements
            are features such as \textbf{Self Starting} and function of the \textbf{Buttons}.
        \end{column}

        \begin{column}{0.48\textwidth}
            \begin{block}{Performance Assessment}
                
            \end{block}
        \end{column}
    \end{columns}

\note{
\huge Austin and Matt (Describe a requirement) \normalsize

\begin{itemize}
 \item Our system also has to perform well, and needs certian features such as auto balancing
 \item self starting
 \item and functioning buttons and controls
\end{itemize}
}

\end{frame}

\subsection{Physical Requirement}
\begin{frame}
    \frametitle{Physical Requirements}

    \begin{columns}
        \begin{column}{0.48\textwidth}
            \begin{block}{Physical Requirements}
                
            \end{block}
        \end{column}

        \begin{column}{0.48\textwidth}
            Physical Requirements are like the other requirements and define the physical
            attributes that define success in solving our product's problem. The most important here
            involve proper use of \textbf{Material} and physical strength requirements.
        \end{column}
    \end{columns}

\note{
\huge Matt and Kat (describes a requirement) \normalsize

\begin{itemize}
 \item There are some phsysical limits to our system as well, it needs to be
 \item made from strong materials
 \item have a long life
 \item and be made from easily replacable, standard components wherever possible
\end{itemize}
}

\end{frame}

\subsection{Risk Assessment}
\begin{frame}
    \frametitle{Risk Assessment}

    \begin{columns}
        \begin{column}{0.48\textwidth}
            Any product or plan comes with risks but mitigation of risks can help make a safe
            and functional product, a couple of the most critical components of our risk assessment
            were safety involving \textbf{Pinch Points}, being \textbf{Struck by moving components}
            or the potential risk of electrical fire due to electronics inside.
        \end{column}

        \begin{column}{0.48\textwidth}
            \begin{block}{Risk Assessment}
                
            \end{block}
        \end{column}
    \end{columns}

\note{
\huge Joe and Matt (describes requiremnt) \normalsize

\begin{itemize}
 \item Its important to consider the risks when designing a product, some of our most important considerations and \textbf{mitigations} are focused around
 \item Pinch points
 \item Moving parts
 \item Electrical hazzards
 \item and damage to the machine by normal training use.
\end{itemize}

\huge Plz no bonk \normalsize
}

\end{frame}

\subsection{Enviormental Requirements}
\begin{frame}
    \frametitle{Environmental Requirements}

    \begin{columns}
        \begin{column}{0.48\textwidth}
            \begin{block}{Environmental Requirements}
                
            \end{block}
        \end{column}

        \begin{column}{0.48\textwidth}
            We know that our product will be used in some environment, if we want to design a safe
            and functional product we need to take this into account, things like \textbf{Usage schedule}
            and the quality of the air we're blowing over our electronics, mitigation of
            \textbf{dust and oils} as well.
        \end{column}
    \end{columns}

\note{
\huge Kat \normalsize

\begin{itemize}
 \item We expect that our product will be used in some enviorment so we've developed requirements to target the sort of situations we think it will be used in
 \item things like planning for dust ingress, skin oils, normal lubrication and air quality
 \item The system should consider vibrations and effects of long term use
\end{itemize}
}

\end{frame}

\subsection{Engineering Standards}
\begin{frame}
    \frametitle{Engineering Standards}

    \begin{columns}
        \begin{column}{0.48\textwidth}
            Designing to existing engineering standards not only reduces work but makes it easier
            for another team or engineer to make modifications, repairs upgrades or ensure future
            interoperability with existing systems.
        \end{column}

        \begin{column}{0.48\textwidth}
            \begin{block}{Engineering Standards}
                
            \end{block}
        \end{column}
    \end{columns}

\note{
\huge Joe's got this one \normalsize

\begin{itemize}
 \item Building to existing engineering standards reduces our workload,
 \item promotes easier servicing in situ,
 \item and makes our product safer by following established guidelines
\end{itemize}
}

\end{frame}

\section{Design Concepts}
\begin{frame}
    \frametitle{Design Concepts (1)}

    \begin{columns}
        \begin{column}{0.48\textwidth}
            \begin{block}{Sketch 1}
                
            \end{block}
        \end{column}

        \begin{column}{0.48\textwidth}
            \begin{block}{Sketch 2}
                
            \end{block}
        \end{column}
    \end{columns}

\note{
\begin{itemize}
 \item Sketch 1 is our inital design concept drawn by Matt <3
 \item Sketch 2 shows how our product may look sizewise compared to a 5'11" person
\end{itemize}
}

\end{frame}

\begin{frame}
    \frametitle{Design Concepts (2)}

    \begin{columns}
        \begin{column}{0.48\textwidth}
            \begin{block}{Sketch 3}
                
            \end{block}
        \end{column}

        \begin{column}{0.48\textwidth}
            \begin{block}{Sketch 4}
                
            \end{block}
        \end{column}
    \end{columns}

\note{
\begin{itemize}
 \item Sketch 3 is another view of our inital 3d model
 \item and sketch 4 shows what our motor and trolley carriage may look like with belt between them
\end{itemize}
}

\end{frame}

\begin{frame}
    \frametitle{Design Concepts (3)}

    

\note{
\begin{itemize}
 \item We're nearing completion with our controller board.
\end{itemize}
}

\end{frame}

\begin{frame}
    \frametitle{Design Concepts (4)}

    \begin{columns}
        \begin{column}{0.48\textwidth}
            \begin{block}{Sketch 5}
                
            \end{block}
        \end{column}

        \begin{column}{0.32\textwidth}
            \begin{block}{Sketch 6}
                
            \end{block}
        \end{column}
    \end{columns}

\note{
\begin{itemize}
 \item Some more design concepts, on the left, a common cam-based belt tensioning method that reduces need to service the belt,
 \item on the right we have the bearing stackup for our carriage.
\end{itemize}
}

\end{frame}

\begin{frame}
    \frametitle{Task Plan}

    With both ProjectLibre (An open source program)

    

    and github task management, we plan and manage our team's productivity.

    

\note{
\huge Kat

its a spreadsheet with time slots \normalsize

\begin{itemize}
 \item We plan everything using ProjectLibre and github task management, Theres a larger copy of our ProjectLibre timeline at the end of the presentation.
\end{itemize}
}

\end{frame}

\section{Budget}
\begin{frame}
    \frametitle{Budget}

    \begin{columns}
        \begin{column}{0.70\textwidth}
            
        \end{column}

        \begin{column}{0.30\textwidth}
            We project to complete our project underbudget! With a low upfront development cost.
            We currently project spending \$250 to \$300 for our prototype.
        \end{column}
    \end{columns}

\note{
\huge Austin \normalsize

\begin{itemize}
 \item So far we project we'll be underbudget, between \$250 and \$300
\end{itemize}
}

\end{frame}

\section{Diagrams}
\subsection{Block Diagrams}
\begin{frame}
    \frametitle{Block Diagram}

    \begin{columns}
        \begin{column}{0.70\textwidth}
            
        \end{column}

        \begin{column}{0.30\textwidth}
            \begin{block}{Block Diagram}
                The block diagram details the electrical, mechanical and software components.
                And their relationship to each other.
            \end{block}
        \end{column}
    \end{columns}

\note{
\huge Matt \normalsize

\begin{itemize}
 \item Our block diagram shows how our software, hardware and electronics may interact in a final system
\end{itemize}
}

\end{frame}

\subsection{Operations}
\begin{frame}
    \frametitle{Operations}

    \begin{columns}
        \begin{column}{0.30\textwidth}
            \begin{block}{Operations}
                The Operations diagram details the physical and general controls.
            \end{block}
        \end{column}

        \begin{column}{0.70\textwidth}
            
        \end{column}
    \end{columns}

\note{
\huge Joe \normalsize

\begin{itemize}
 \item The operations chart details our physical and general controls like the tft screen
 \item the buttons
 \item the motor controller and encoders
\end{itemize}
}

\end{frame}

\subsection{Software}
\begin{frame}
    \frametitle{Software Flowchart}

    \begin{columns}
        \begin{column}{0.72\textwidth}
            
        \end{column}

        \begin{column}{0.28\textwidth}
            \begin{block}{Software Flowchart}
                The software flowchart is an overview of all the software functions of our
                proposed product.
            \end{block}
        \end{column}
    \end{columns}

\note{
\huge Austin \normalsize

\begin{itemize}
 \item Our software flowchart details how the PID control scheme will be interactable by the users
\end{itemize}
}

\end{frame}

\section{End}
\begin{frame}
    \frametitle{End}

    \begin{block}{}
        \begin{center}
            \Huge Questions and Comments?
        \end{center}
    \end{block}

    \begin{center}
        Find the source code for this document, and the rest of our designs, firmware, hardware
        and notes on GitHub!

        
    \end{center}

\note{
\begin{itemize}
 \item So please if you have any questions we would love to hear them.
 \item All of our software, CAD, hardware and design docs are licensed under
 \item \huge The MIT Open Source License \normalsize and available via git.
 \item If you have a specific slide in mind we can go back to it!
\end{itemize}
}

\end{frame}

\section{Appendices}
\begin{frame}
    \frametitle{References}

    
\end{frame}

\begin{frame}
    \frametitle{Complete Timeline}

    
\end{frame}

\begin{frame}
    \frametitle{Calculations}

    

    Octave math model.
\end{frame}

\end{document}

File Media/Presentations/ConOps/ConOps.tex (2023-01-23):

\documentclass{article}

\usepackage[utf8]{inputenc}

\usepackage{graphicx}
\graphicspath{ {./Resources/} }

\title{ConOps - Inverted Pendulum PID Controller}       % Title
\author{Austin, Joe, Matt, Kathryn}                     % Team members
% \institute{SNHU/CETA}                                   % Institute
% \logo{\includegraphics[height=0.8cm]{../../AJMK_Logo}}  % Our Logo

\begin{document}

\maketitle % Draw the title page

\section{Stakeholders}

Stakeholders are the people and organizations who have a stake or say in the actual
implementation and review of our proposed system, these include:

\begin{itemize}
    \item Educators and Acedemics,
    \item Industrial Training
    \item Producers of parts and service
\end{itemize}

\section{System Description}

A PID system is a general method for a computer or intelligent system to reduce the error
or deviation in a system. Examples include the thermostat in a stove, the cruise control in a
car or the gain control on a phone microphone.

This system aims to help display the fundamentals of a PID system in the form of a machine dedicated
to allowing the operator to experiment with the tuning and functions behind the algorithm.

It will be constructed from steel and wood, powered by a single motor and a small processor
and power supply, portable but robust enough to be installed in semi-permanent use.
Weighing between 40 and 70lb, with a tft screen. The system will use a demo PID loop to
balance an inverted pendulum and allow user input to control the rates and response of the loop.

\section{Operational Environment}

This demonstrator will be in a:

\begin{itemize}
    \item High traffic environment
    \item Possibly dusty
    \item Indoors
    \item Powered on 24/7
\end{itemize}

The enviorment the unit is placed in will affect the Support Enviorment.

\section{Support Environment}

This demonstrator will be made from as many COTS (Common Off The Shelf) parts
as possible to ensure simple replacement.

The enviorment the unit is in will affect many parts of this demonstrator

\begin{itemize}
    \item Wearing components (belts, sliders)
    \item[Mitigation] All wearable parts will be accesable and removable without major dissasembly.
    \item Constant touching and interaction
    \item[Mitigation] The demonstrator will be built from sturdy and easy to clean components.
    \item Constant uptime
    \item[Mitigation] Low power/sleep mode can prolong the life of electronics when not in use
\end{itemize}

Anything requiring major dissasembly, prolonged repair or specailaty parts will be built robust and
within manufacturer spec with documentation alongside. All systems either self calibrating or
not requiring calibration. The system will be designed with long life servicibility in mind.

\section{Operating Modes}
% Operating modes goes here

\begin{itemize}
    \item Off mode: the state in which the system is powered down and or unplugged.
    \item Idle mode: a power saving mode in which fans are turned off; the TFT screen is turned off; and the motor controller, CPU, and power supply will be swapped to their internal lower power consumption mode.
    \item Spin-up mode: a custom control procedure that self initializes (swing the pendulum up into a ready state using harmonic oscillation.
    \item Demo PID mode: a build-in PID procedure with lock Kp, Ki, and Kd values to demonstrate how the inverse pendulum is properly balanced.
    \item User PID mode: a control structure in which the user can manipulate the Kp, Ki, and Kd constants to witness the effects of their changes on the stability of the pendulum.
\end{itemize}

\section{Use}

This system will provide an excellend robust teaching tool for its users to grasp and deeply
understand the function of a PID loop, witch is an essential software and hardware algorithm
for many industries.

\section{Risks}

This system introduces risks

\begin{tabular}{ |p{1.5cm}|p{1.5cm}||p{3cm}|p{6cm}|  }
    \hline
    Likelyhood & Severity & Risk                                       & Mitigation           \\
    \hline
    10         & 8        & Pinch Points and swinging pendulum         & Capacitive e-stop
    technology as well as sound alerts when the system begins to move, and a
    transparent shield / cover to isolate the dynamic system.                                 \\
    \hline
    2          & 5        & Failure in-situ                            & Easily serviceable
    parts.
    \\
    \hline
    2          & 2        & Damaged to the unit from normal use        & Software locks, an
    e-stop switch, and a rubber bumper / mechanical hard stops.
    \\
    \hline
    1          & 5        & Short circuits and electrical malfunctions & Have a fused power
    supply, and will follow IEC standards with proper grounding.
    \\
    \hline
    3          & 5        & Heat                                       & Embedded fans in the
    storage with plenty of holes for ventilation.
    \\
    \hline
\end{tabular}

\section{Impact Considerations}

There are some considerations to think about with the implementation of this
sytem, such as

\begin{itemize}
    \item Being a hazzard and risking misuse.
    \item Requiring physical space, either for storage or use.
    \item Producing a significant amount of polutant to construct, deploy, and
          eventually recycle/throw away.
\end{itemize}

\pagebreak
\section{Inital Renders}


\vspace{1cm}






\vspace{1cm}


\end{document}

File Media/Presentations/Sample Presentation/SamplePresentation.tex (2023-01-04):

\documentclass{beamer}

\usepackage[utf8]{inputenc}
\usetheme{Madrid}
\usecolortheme{beaver}

\usepackage{graphicx}
\graphicspath{ {./Resources/} }

% Title here
\title{Sample Presentation}
\author{Unamed Team}
\institute{SNHU/CETA, EG-310}

\begin{document}

\frame{\titlepage} % Draw the title page

% A frame
\begin{frame}
\frametitle{Sample frame 1}

% Some columns
\begin{columns}
    \begin{column}{0.48\textwidth}
        \begin{block}{Cute critter}
            What is this thing?
        \end{block}
    \end{column}
    \begin{column}{0.48\textwidth}
        
    \end{column}
\end{columns}

\end{frame}

% A frame
\begin{frame}
\frametitle{Sample frame 2}



\begin{block}{Fops}
    He has failed.
\end{block}

\end{frame}

\end{document}

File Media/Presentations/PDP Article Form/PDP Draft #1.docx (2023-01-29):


# Inverted Pendulum PID Demonstrator

Project Development Plan (PDP)

Matt Handley, Joseph Sedutto, Austin Cardosi, Kathryn Swineford

Southern New Hampshire University

# Roles

Team Member | Primary Role | Secondary Role
Matt Handley | CAD | Calculations
Joe Sedutto | Electrical | Machining
Kat Swineford | Documentation | Assembly
Austin Cardosi | Coding | File Organization

Table 1.1.1

# Abstract

A PID loop (Proportional, Integral, Derivative) loop is a very common error-reducing algorithm in our modern world. It can be implemented in many different ways, and controls everything from the heating cycle of your toaster, to the cruise control in your car.

The PID loop seeks to reduce the “error” in a system, that error may be the speed you want to go, the target temperature of your toast or the upright position of a pendulum. Because PID is used so extensively, and is somewhat difficult to grasp from a purely numeric perspective, a PID demonstrator is a tool that allows users to interact with and gain a deeper understanding of the underlying control mechanisms.

This PID demonstrator tackles this problem, it uses robust but minimalist construction to create a high quality and easy to maintain demonstrator, users interact with its front panel to tune and de-tune a system managed by PID, a classic inverted pendulum which is a feat many can relate to, balancing a baseball bat on their finger. Its high moment of inertia allows the pendulum to swing and waver when untuned, yet hold perfectly still when tuned correctly.

# Table of Contents

Roles 2

Abstract 3

Table of Contents 4

Table of Figures 5

Table of Tables 5

The System Description 7

Problem Statement 7

Design Research 7

Rotary Inverted Pendulum 7

Reaction Wheel Inverted Pendulum 8

Technical Challenges 8

Customers/markets/economics/applications 9

Concept of Operations 9

Statements 9

System Requirements (Top Level) 12

Functional Requirements: (what it does) 12

Performance Requirements: (how well it does) 13

Physical Requirements: (sizes, weight) 14

Environmental and Safety Requirements: 14

Engineering Standards: 15

Risk Assessments 15

Risk Assessment 15

Design Concepts 17

Sketches 17

System Composition Block Diagram 19

Flow Chart of Operations 20

Software Flow Chart 21

Health and Safety Design Features: 22

Used Engineering Standards: 22

Task Plan 23

Budget/BOM 24

References 25

Appendixes: 26

Appendix A: Calculations / Model 26

Appendix B: LibreOffice Schedule 27

# Table of Figures

Figure 1.2.1 Rotary Inverted Pendulum……………………………………………………………. 6

Figure 1.2.2 Reaction Wheel Inverted Pendulum…………………………………………………. 7

Figure 5.1.1 Blender Scale Model………………………………………………………………….16

Figure 5.1.2 Blender Full Model…………………………………………………………………… 16

Figure 5.1.3 Carriage Drawing…………………………………………………………………….. 16

Figure 5.1.4 Blender Motor Close-Up Model……………………………………………………... 16

Figure 5.1.5 Belt Tensioning Cam Drawing………………………………………………………. 17

Figure 5.1.6 Early Design Sketch………………………………………………………………….. 17

Figure 6.1.1 System Composition Block Diagram……………………………………………….. 17

Figure 6.2.1 Flow Chart of Operations……………………………………………………………. 18

Figure 6.3.1 Software Flowchart…………………………………………………………………… 18

Figure 7.1.1 Task Plan……………………………………………………………………………… 23

Figure 8.1.1 Bill of Materials……………………………………………………………………….. 24

Figure 9.1.1 Calculations/Model…………………………………………………………………… 26

# Table of Tables

Table 1.1.1 Team Roles………………………………………………………………………………. 2

Table 3.1.1 Functional Requirements……………………………………………………………... 12

Table 3.2.1 Performance Requirements………………………………………………………….. 12

Table 3.3.1 Physical Requirements……………………………………………………………….. 13

Table 3.4.1 Environmental Requirements………………………………………………………… 14

Table 3.5.1 Engineering Standards………………………………………………………………... 14

Table 4.1.1 Risk Assessment……………………………………………………………………….15

# The System Description

## Problem Statement

The goal is to make a PID Demonstrator that is intuitive for all age groups to demonstrate how to use a PID loop and what each individual variable does to effect a vertical standing pendulum.

## Design Research

#### Rotary Inverted Pendulum

The rotary inverted pendulum spins about a fixed central axis that at the end of the attached fixed point has the pendulum. The combination of motor and sensors allow the pendulum to stand itself upright. Based on the pendulum's angle the motor can accelerate in both directions to counterbalance the falling rod. The example below according to the author cost from 200 to 500 dollars depending on the parts and modifications.


(Figure: 1.2.1)

#### Reaction Wheel Inverted Pendulum

The Reaction Wheel inverted pendulum functions off torque by a spinning wheel at the top of the pendulum. The torque and counter-torque used to move the pendulum left or right can allow for the pendulum to have the ability to stand vertically when the PID loop is corrected. This specific example was made with a variety of lego parts and the builder later in the video demonstrates that his loop works with a variety of weights and modifications.

(Figure: 1.2.2)


#### Technical Challenges

Challenges that will face the system we are trying to make tuning the pendulum to stay vertical as PID loops can be testy to get right. A potential solution for this is to spend more time perfecting the loop after construction. Another problem that might occur will be to get the pendulum to swing up automatically without any outside assistance. A potential solution for this is to find examples of this kind of pendulum and see how to possibly code a start up sequence. Last problem that might occur is troubleshooting the sensors to ensure accurate and precise readings for demonstrating the graphs of the PID loop. This can be mitigated by testing the sensors prior to mounting them to the system.

## Customers/markets/economics/applications

Demonstrates control systems using a PID loop. Allows users to vary the control loop constants to change the behavior of the pendulum. Educational application for academia and industry.

# Concept of Operations

## Statements

Stakeholders: Southern New Hampshire University, Professor Carlstrom, Professor Husson, Professor Guo, educators and academics, industrial training, producers of parts and service.

Users: Pendulum team, educators and academia, industrial and software training, and producers of parts and service.

System Description: A PID system is a general method for a computer or intelligent system to reduce the error or deviation in a system. Examples include the thermostat in a stove, the cruise control in a car or the gain control on a phone microphone.

This system aims to help display the fundamentals of a PID system in the form of a machine dedicated to allowing the operator to experiment with the tuning and functions behind the algorithm.

It will be constructed from steel and wood, powered by a single motor and a small processor and power supply, portable but robust enough to be installed in semi-permanent use. Weighing between 30 and 50lb, with a tft screen. The system will use a demo PID loop to balance an inverted pendulum and allow user input to control the rates and response of the loop

Operational Environment: This demonstrator will be in a high traffic environment, that is possibly dusty. It will be located indoors, and will be powered 24/7.

Support Environment: This demonstrator will be made from as many COTS (Common Off The Shelf) parts as possible to ensure simple replacement. The environment the unit is in will affect many parts of this demonstrator

• Wearing components (belts, sliders)

Mitigation all wearable parts will be accessible and removable without major disassembly.

• Constant touching and interaction

Mitigation the demonstrator will be built from sturdy and easy to clean components.

• Constant uptime

Mitigation low power/sleep mode can prolong the life of electronics when not in use

Anything requiring major disassembly, prolonged repair or specialty parts will be built robust and within manufacturer spec with documentation alongside. All systems either self calibrating or not requiring calibration. The system will be designed with long life serviceability in mind.

Operating Modes:

• Off mode: the state in which the system is powered down and or unplugged.

• Idle mode: a power saving mode in which fans are turned off; the TFT screen is turned off; and the motor controller, CPU, and power supply will be swapped to their internal lower power consumption mode.

• Spin-up mode: a custom control procedure that self initializes (swing the pendulum up into a ready state using harmonic oscillation.

• Demo PID mode: a built-in PID procedure with lock Kp, Ki, and Kd values to demonstrate how the inverse pendulum is properly balanced.

• User PID mode: a control structure in which the user can manipulate the Kp, Ki, and Kd constants to witness the effects of their changes on the stability of the pendulum.

Use: This system will provide an excellent robust teaching tool for its users to grasp and deeply understand the function of a PID loop, which is an essential software and hardware algorithm for many industries.

Risks:

• Pinch Points and swinging pendulum

• Failure during demonstrations

• Damaged to the unit from normal use

• Short circuits and electrical malfunctions

• Heat accumulation

Impact Consideration: There are some considerations to think about with the implementation of this system:

• Being a hazard and risking misuse.

• Requiring physical space, either for storage or use.

• Producing a significant amount of pollutant to construct, deploy, and eventually recycle/throw away.

# System Requirements (Top Level)

## Functional Requirements: (what it does)

Number | Requirement | Verification
1.1 | The system shall have a low power mode in which all components are put into an idle state. | Feature/Test/ Inspection
1.2 | The system shall have an autonomous mode in which the pendulum will balance itself using an integrated PID loop. | Feature/ Demonstration
1.3 | The system shall have a user-control mode in which the turning of potentiometers shall manipulate the constants of the PID loop | Feature/ Demonstration
1.4 | The system shall be self-tensioning. | Feature/ Inspection/Test
1.5 | System modes will be selectable by the user. | Feature/ Demonstration
1.6 | The system shall have a screen capable of displaying the oscillations of the pendulum and the correction curve formed by the PID loop to the user. | Feature/ Inspection/ Demonstration
1.7 | The system shall have a capacitive sensor that detects if the pendulum has come in contact with human skin. | Feature/Test
1.8 | The system shall have an emergency stop. | Feature/Test/ Inspection
1.9 | The system shall have a buzzer or noise making component to warn users of before the pendulum begins to harmonically oscillate into its balanced position. | Feature/ Demonstration
1.10 | The system shall have an embedded fan in the electrical compartment to cool the circuit board and the power supply. | Feature/Test

Table 3.1.1

## Performance Requirements: (how well it does)

Number | Requirement | Verification
2.1 | System should be reasonably quiet. | Test/ Demonstration
2.2 | The system shall be sufficiently powered using a standard 120 V wall outlet. | Test/Feature
2.3 | The pendulum shall swing up into a start position in under 15 seconds. | Test/ Demonstration
2.4 | Upon sensing a ground due to the touch of human skin, the capacitive sensor in the circuit board shall cut current from reaching the motor in under 200ms. | Test/ Demonstration/ Feature
2.5 | Upon the press of the estop, the system shall cut current from reaching the motor instantly. | Test/Inspection
2.6 | The autonomous mode shall balance the pendulum for the entirety of the duration that the system is in this mode (after the pendulum has been spun up to its starting position). | Test/ Demonstration
2.7 | No component shall not exceed a temperature of 110 degrees Fahrenheit while in normal operation. | Test/Inspection

Table 3.2.1

## Physical Requirements: (sizes, weight)

Number | Requirement | Verification
3.1 | The pendulum shall weigh between 8 to 13 grams | Inspection
3.2 | The span of the linear track for the pendulum shall be no more than three feet long. | Inspection
3.3 | The display screen shall have color to easily distinguish between the control loop, the current error in the system, and the target value for achieving balance. | Test/ Demonstration/ Inspection
3.4 | The system shall weigh no greater than 50 lbs with the removable legs attached. | Inspection
3.5 | The frame of the assembly shall be made with mild steel. | Inspection/ Feature
3.6 | All electrical components shall be grounded. | Inspection/ Test
3.7 | The pendulum shall be 1.5 feet in length. | Inspection
3.8 | All elements shall operate under their yield stresses and have a factor of safety of 1.5 or greater for embedded components. | Inspection/ Feature
3.9 | All elements shall be under a fatigue strength that allows for a product lifetime of 20 years. | Inspection/ Feature

Table 3.3.1

## Environmental and Safety Requirements:

Number | Requirement | Verification
4.1 | The wooden base shall be given a varnish finish to improve the longevity of the wood and stop corrosion and thermal cycling damage. | Inspection
4.2 | All fasteners shall be secured from vibration. | Inspection/ Feature
4.3 | The system shall operate in a temperature range from 50 degrees Fahrenheit to 90 degrees Fahrenheit. | Inspection/ Test
4.4 | The electrical compartment in the base shall be to open independently of the system in order to remove any dust that accumulates. | Test/ Demonstration

Table 3.4.1

## Engineering Standards:

Number | Requirement | Verification
5.1 | IEC TR 61923: IEC standards for instruments in household/indoor environments | Inspection/ Test
5.2 | IEC 60745: IEC standard for power tools and similar motor controlled appliances | Inspection/ Test
5.3 | IEC 60364-1: Rules for general design (fuses, proper grounding, insulation) | Inspection/ Test

Table 3.5.1

# Risk Assessments

## Risk Assessment

Risk Statement | Likelihood | Consequence | | Mitigation | Trigger
| | Tech | Cost Schedule
Operators can have hair, fingers or extremities caught in pinch points. | 5 | Low | Low | Shields and guards keep hair and fingers away from dangerous areas. Capacitive and e-stop sensors deactivate loop when out of spec | On touch
Operators may become struck by falling pendulum | 1 | Low | Low | Pendulum has a very low weight and a low maximum jerk-speed. | On touch
Machine can become damaged by improper tuning | 3 | High | Low | When out of tune PID loops are prone to vibration and oscillation, to mitigate we will - Program min and max safe values - Build with the understanding that out of tune loops will produce known vibrations | When in use
Risk of fire, or total failure | 1 | Low | Low | Well documented internals and an electrical system robust and built to common standards. | All the time.

Table 4.1.1

# Design Concepts

## Sketches


Fig 5.1.1 | Fig 5.1.2


Fig 5.1.3 | Fig 5.1.4


Fig 5.1.5 | Fig 5.1.6

## System Composition Block Diagram


Figure 6.1.1

## Flow Chart of Operations


Figure 6.2.1

## Software Flow Chart


Figure 6.3.1

## Health and Safety Design Features:

- Protective shielding around the pendulum’s range of motion to avoid pinch points and physical contact.
- Capacitive e-stop and manual e-stop in case of emergency.
- All electrical components are grounded to prevent dangerous discharge.
- All components shall be ventilated and fan cooled to regulate temperatures.
- Access to embedded components shall be easy to clean the machine and remove dust and debris.

## Used Engineering Standards:

- EC TR 61923: IEC standards for instruments in household/indoor environments
- IEC 60745: IEC standard for power tools and similar motor controlled appliances
- IEC 60364-1: Rules for general design (fuses, proper grounding, insulation)

# Task Plan


Figure 7.1.1

# Budget/BOM


(https://github.com/KenwoodFox/EG-310-InvertedPendulum/blob/feat/PDP_draft_%231/Media/Notes/Pendulum328BOM.csv)

Figure 8.1.1

# References

Figure (1.2.1) (n.d.). Rotary Inverted Pendulum. Quanser. Retrieved January 22, 2023, from

https://www.quanser.com/wp-content/uploads/2017/03/ROTPEN-graphics.jpg

Figure (1.2.2) (n.d.). Lego, Raspberry and Python Project - Reaction Wheel Inverted Pendulum.

(2022, April 16). YouTube. Retrieved January 22, 2023, from https://youtu.be/WObG2LoSEwQ

# Appendixes:

## Appendix A: Calculations / Model


Figure 9.1.1

## Appendix B: LibreOffice Schedule


SNHU, CETA 2023, January

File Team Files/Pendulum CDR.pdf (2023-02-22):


# Inverted Pendulum PID Demonstrator

## Critical Design Review (CDR)

Matt Handley, Joseph Sedutto, Austin Cardosi, Kathryn Swineford

Southern New Hampshire University

Junior Engineering Design EG-310-20805 Spring 2023

February 12, 2023

# Table of Contents:

Table of Contents: | 2
Concept of Operations Summary: | 3
Summary of Trade Studies: | 6
Requirements Compliance: | 7
Functional: | 7
Performance: | 8
Interface, Design, Resource: | 9
System Design and Properties: | 10
System Functional Block Diagram: | 11
System Operational Flowchart: | 11
Subsystem Definition: | 12
Subsystem Design Details: | 12
Subsystem 1 or Mechanical | 12
Subsystem 2 or Electrical | 13
Subsystem 3 or Software | 14
Public health, safety, and welfare | 15
Global, cultural, social, environmental, and economic factors | 15
Summary of Prototype Activities: | 16
Prototype Mainboard | 16
Prototype Bearings | 17
Summary of Analyses: (Feasibility Tests) | 18
Bearings | 18
Board Design | 18
Calibration and Maintenance Plan: | 18
Phase-D Readiness (Go Over Data Package List): | 19
Ethical and Professional Responsibilities: | 19
Safety: | 20
Impact Considerations: | 21
References: | 21
Appendix: | 22

## Concept of Operations Summary:

Stakeholders: Southern New Hampshire University, Professor Carlstrom, Professor

Husson, Professor Guo, educators and academics, industrial training, producers of parts and

service.

Users: Pendulum team, educators and academia, industrial and software training, and

producers of parts and service.

System Description: A PID system is a general method for a computer or intelligent

system to reduce the error or deviation in a system. Examples include the thermostat in a stove,

the cruise control in a car or the gain control on a phone microphone.

This system aims to help display the fundamentals of a PID system in the form of a

machine dedicated to allowing the operator to experiment with the tuning and functions behind

the algorithm.

It will be constructed from steel and wood, powered by a single motor and a small

processor and power supply, portable but robust enough to be installed in semi-permanent use.

Weighing between 30 and 50lb, with a TFT screen. The system will use a demo PID loop to

balance an inverted pendulum. Users will have the ability to adjust the input rates while

observing the response of the loop to course correct the pendulum.

Operational Environment: This demonstrator will be in an engineering lab setting that

may be exposed to dust over time. This is an indoor device and can be powered on and off for

demonstrations as necessary.

Support Environment: This demonstrator will be made from as many COTS (Common

Off The Shelf) parts. This will allow for simple replacement when and if things break down. The

environment the unit is in and the frequency of which the equipment is run will affect many parts'

life cycles.

- Wearing components (belts, sliders)

Mitigation all wearable parts will be accessible and removable without major

disassembly.

- Constant touching and interaction

Mitigation the demonstrator will be built from sturdy and easy to clean components.

- Constant uptime

Mitigation low power/sleep mode can prolong the life of electronics when not in use

Anything requiring major disassembly, prolonged repair or specialty parts will be built

robust and within manufacturer spec with documentation for reference. All systems either self

calibrating or not requiring calibration. The system will be designed with long life serviceability in

mind.

Operating Modes:

- Off mode: the state in which the system is powered down and or unplugged.
- Idle mode: a power saving mode in which fans are turned off; the TFT screen is turned

off; and the motor controller, CPU, and power supply will be swapped to their internal lower

power consumption mode.

- Spin-up mode: a custom control procedure that self initializes (swing the pendulum up

into a ready state using harmonic oscillation.

- Demo PID mode: a built-in PID procedure with lock Kp, Ki, and Kd values to

demonstrate how the inverse pendulum is properly balanced.

- User PID mode: a control structure in which the user can manipulate the Kp, Ki, and Kd

constants to witness the effects of their changes on the stability of the pendulum.

Use: This system will provide an excellent robust teaching tool for its users to grasp and

deeply understand the function of a PID loop, which is an essential software and hardware

algorithm for many industries.

Risks:

- Pinch Points and swinging pendulum
- Failure during demonstrations
- Damaged to the unit from normal use
- Short circuits and electrical malfunctions
- Heat accumulation

Impact Consideration: There are some considerations to think about with the

implementation of this system:

- Being a hazard and risking misuse.
- Requiring physical space, either for storage or use.
- Producing a significant amount of pollutant to construct, deploy, and eventually

recycle/throw away.

## Summary of Trade Studies:

All weights equal unless specified otherwise. | User Interaction Methods
Buttons Only | Buttons and LEDs | Buttons and TFT | Buttons, Buzzer, TFT
Demonstrates effectively machine state | -- | - | * | +
Provides easy to use selection of mode | * | * | * | *
Provides meaningful feedback about PID Performance | -- | * | * | +
Is an effective educational tool/in the spirit of the product | -- | - | * | +
All weights equal unless specified otherwise. | Bearings
No Bearings | Dry Bearings | Ball Bearings
Conforms to minimum req’ for vibration, stiffness, and cost. | -- | + | *
Easily sourceable/ Requires lower maintenance | * | * | -
Operates silently | - | - | *
Requires little replacement maintenance/ | -- | - | *
All weights equal unless specified otherwise. | Motor choice
DC Motor | Stepper Motor | Servo Motor
Low Noise | * | - | +

Ease of replacement maintenance/ | - | * | --
High Performance | -- | - | +
Low cost | + | * | --

## Requirements Compliance:

### Functional:

Req ID or Section | Req. Title | Subject Statements | Req. Value | Performance | Margi n | Notes / Basis
1.1 | Low Power Mode | Provide low power mode in which all components are put into an idle state. | 150 mA of current | 50 mA of current | [10%]
1.2 | Autonomous Mode | Provide self-balancing autonomous mode. | 30 minutes | Continuously | [15%]
1.3 | User-Control Mode | Provide user-control mode in which pendulum behavior is manipulated by variable resistors. | P Term is variable | P, I and D are variable | [N/A]
1.4 | Self-Tensioning | The system shall be self-tensioning. | Belt Always Taunt | [Comply / Does Not Comply] | [N/A]
1.5 | Mode Selection | System modes will be selectable by the user using a button. | Usage of Push Button | [Comply / Does Not Comply] | [N/A]
1.6 | User Control | The system shall have a display method capable of displaying the oscillations of the pendulum and the correction curve formed by the PID loop to the user. | Describe the error in the loop in a meaningful way. | Display the error in the loop as well as system state, score and PID values. | [5%]
1.7 | Capacitive E-stop | Provide a capacitive e-stop built into the circuit board. | E-Stop reacts when touched. | [Comply / Does Not Comply] | [N/A] | Sweaty skin vs. dry skin?

1.8 | Manual E-stop | The system shall have a manual emergency stop. | E-Stop reacts when pressed. | [Comply / Does Not Comply] | [N/A]
1.9 | Warning Buzzer | The system shall have a buzzer to warn the user of the pendulum’s harmonic oscillations into a ready state. | Buzzer functions on mode change. | [Comply / Does Not Comply] | [N/A]
1.10 | Fan for Power Supply | Provide an embedded fan for the power supply. | Fan is adequate for emitted heat. | Fan is more than adequate for emitted heat. | [10%]
1.11 | TFT Mode Display | The TFT screen shall display the system’s current mode. | TFT displays current mode. | [Comply / Does Not Comply] | [N/A]
1.12 | TFT PID Constant Display | The TFT screen shall display the PID loops current Kp, Ki, and Kd values. | TFT displays constants | [Comply / Does Not Comply] | [N/A]

### Performance:

Req ID or Section | Req. Title | Subject Statements | Req. Value | Performance | Margi n | Notes / Basis
2.1 | Power Required | Fully powered using a standard 120 V wall outlet. | 120 V | [Comply / Does Not Comply] | [N/A]
2.2 | Spin-Up | The pendulum shall swing up into a start position in under 15 seconds. | 20 s | 15 s | [10%]
2.3 | Capacitive E-Stop | Capacitive estop shall cut current from the motor in under 200 ms | <= 200 ms | [Comply / Does Not Comply] | [N/A]
2.4 | Manual E-Stop | Upon the press of the estop, the system shall cut current from reaching the motor instantly | <= 30ms | <= 15 ms | [N/A]
2.5 | System Temp. | No component shall not exceed a temperature of 110 degrees Fahrenheit while in normal operation. | 110 degrees F | 90 degrees F | [20%]

### Interface, Design, Resource:

Req ID or Section | Req. Title | Subject Statements | Req. Value | Performance | Margi n | Notes / Basis
3.1 | Mass | The pendulum shall weigh between 8 to 13 grams | 13 g | 10 g | [10%]
3.2 | Span | The span of the linear track shall be no more than three feet long. | 3 ft | 2.5 ft | [N/A]
3.3 | Interface | The display screen shall have color to easily distinguish between the control loop, the current error in the system, and the target value for achieving balance. | Easily legible | [Comply / Does Not Comply] | [N/A]
3.4 | Weight | The system shall weigh no greater than 50 lbs with the removable legs attached. | 50 lbf | 40 lbf | [10%]
3.5 | Frame Material | The frame of the assembly shall be made with mild steel. | Mild Steel | [Comply / Does Not Comply] | [N/A]
3.6 | Design | All electrical components shall be grounded. | Grounded to meet Standards | [Comply / Does Not Comply] | [N/A]
3.7 | Length | The pendulum shall be no greater than 1.5 feet in length. | 1.5 ft | 1.4 ft | [N/A]
3.8 | Factor of Safety | All elements shall operate under their yield stresses and have a factor of safety of 1.5 or greater for embedded components. | 1.5 | [Comply / Does Not Comply] | [N/A]
3.9 | Design | All elements shall be under a fatigue strength that allows for a product lifetime of 20 years. | Appropriate σ | [Comply / Does Not Comply] | [N/A]
3.10 | Design | Wooden base shall have varnish applied. | Apply varnish | [Comply / Does Not Comply] | [N/A]
3.11 | Design | All fasteners shall be secured from vibration. | Apply loctite | [Comply / Does Not Comply] | [N/A]

## System Design and Properties:


## System Functional Block Diagram:


## System Operational Flowchart:

## Subsystem Definition:

- Mechanical
- Electrical
- Software

## Subsystem Design Details:

Product consists of one main system that can be further expanded into three subsystems. The

three subsystems are mechanical, electrical, and software. These subsystems are dependent

on one another. For the system to successfully operate all subsystems must successfully

communicate with one another. In the following sections, A description for each subsystem will

be listed - such as its functions, diagrams, etc.


### Subsystem 1 or Mechanical

The mechanical subsystem consists of the physical parts in the product such as rods, motors,

pendulum, etc. Below is a basic overview of how the mechanical subsystem operates. :


### 1. Motor

a. The motor is turned and is connected to the belt in which it can either accelerate

or decelerate.

### 2. Belt

a. Allows for the Movement of the carriage to allow for the PID loop to balance the

pendulum

### 3. Carriage

a. Connects to the belt, linear rails, and pendulum. Provides the ability to use the

belt and motor to balance the pendulum.

### 4. Pendulum

a. Rod attached to the carriage. Allows for movement in two directions along the

same directions of the linear rails the carriage is attached to for the PID loop to

balance it.

The software/program subsystem is what is used to activate the motor. The software subsystem

is further described in the following sections

### Subsystem 2 or Electrical

The electrical subsystem consists of wires, outlets, switches, and all other electrical components

in the product. Some of the important elements involved in the circuitry are. :

- Emergency Stop
- Designed to cut all electric flow from our circuit if turned on
- Power Button
- Has ability to be pressed on and off run and stop system
- Toggle
- Used to switch between operating modes
- Power Source
- Standard 120V outlet

The electrical subsystem is what provides the input to our software subsystem.

### Subsystem 3 or Software

The software subsystem is how the electrical subsystem communicates to the mechanical

subsystem. It consists of all the code that will be implemented in the product. The way the

software subsystem operates is it is able to take data based on which switches are activated

and can control the motor speed and mode accordingly. The software can be further broken

down into three modes, described below. The modes are controlled by a button.

- Low Power Mode
- This mode is the default mode when the system is first turned on.
- Designed to draw little power while the system is not physically moving
- Autonomous Mode
- Designed to self stabilize the pendulum
- Uses harmonic oscillations
- User Controlled Mode

- Awaits input from user

We will also be implementing a TFT screen that is going to be capable of displaying the current

values the motor is drawing.

## Public health, safety, and welfare

One concern for public health in the design is the swinging pendulum itself which can hit and

hurt someone if not used properly or tamper with the safety mechanisms in place on the system.

The safety mechanism in place is a hard stop button if the system malfunctions. It serves to stop

the system cold as well as a mechanism to detect if the pendulum hits something such that it will

stop the system as well. In addition to those factors, a screen between the user and the

swinging pendulum will be implemented. Another concern is the electronics inside overheating

and causing fire. This is presented by the operation conditions to be placed in a lab room. To

combat this the system has very low voltage running it such that overheating causing damage

or fire is unlikely even with constant use.

### Global, cultural, social, environmental, and economic factors

Since the system does use electricity, depending where that power comes from it contributes to

the cost of fossil fuels or other environmental power hazards potentially if left constantly on. It is

to note however this system draws very little electricity compared to other things in the building it

is placed in but nonetheless does draw power. When the system is scrapped, if not ethically

recycled can cause environmental hazards such as releasing toxic chemicals including lead,

mercury, cadmium, and chromium where heavy metals like those can do a great deal of harm.

## Summary of Prototype Activities:

## Prototype Mainboard

Mainboard requires several important features:

- E-Stop
- Button Inputs
- Potentiometers
- Encoder
- Motor output
- Limit Switch
- TFT Screen

The prototype board implements all these features as well as…

- USB Programming/debugging
- Status lights
- Mode and start select buttons
- Onboard VRM
Prototype Activity # | Prototype Activity Description | Data Gathered | Performed By
1 | General Board Function | Board has no obvious faults (missing traces, overvolt etc) | Joe
2 | USB Debugging | Usb debugging and auto-reset works on the devboard | Joe
3 | Encoder Limit Detection | Both chosen interrupts trigger on the rising edge without issue on the devboard | Joe
4 | TFT Screen | TBD | Joe

5 | Buttons and debouncing

Button debouncing
works in software and
hardware on the
devboard

Joe

## Prototype Bearings

See Summary of Trade Studies for specific details and weights.

Each bearing is tested and evaluated with the above chart, with specific attention to:

- Cost of bearing (4 needed for every pendulum)
- Noise (Minimize sliding grinding noises)
- Performance (How well does it slide and protect the carriage shafts)
- Longevity (How long does it last without service or lube?)

Prototype Activity # | Prototype Activity Description | Data Gathered | Performed By
1 | Characterize relative sound levels under operation and gauge their change over time.
2 | Evaluate heat, overall slop, noise and other performance metrics (defined above)
3 | Weight

## Summary of Analyses: (Feasibility Tests)

## Bearings

Results from experimentation with different 8mm bearings.

## Board Design

Results from preliminary board design

## Calibration and Maintenance Plan:

- The system shall perform a self-test on start-up. Due to the pendulum hanging towards

the center of the earth due to gravity, the encoder on the pendulum will be zeroed using

the position.

- The motor shall move towards a limit switch at a set slow speed until it triggers one of

the two limit switches on either side of the linear rails, upon triggering one, the carriage

will then move a set amount of motor steps to the middle of the span of the linear rails.

- All fasteners shall have their tightness ensured before operation, and any renewal of

lubrical for the pendulum shall be performed.

- A maintenance and component replacement manual shall be created in order to easily

explain how to replace the COTS (common of the shelf) parts such as the precision belt

or the motor internals.

## Phase-D Readiness (Go Over Data Package List):

- All drawings and assemblies are on the latest revision and meet all specifications
- All required parts will be ordered through Carlstrom / Joe Donovan this week (2/22/2023)
- Manufacturing of the frame will begin as soon as the steel is delivered, and prototyping

of parts will begin once all remaining parts are delivered.

- Drawings and assemblies will be finalized this weekend (2/25/2023 for machining to

begin.

## Ethical and Professional Responsibilities:

Honesty and integrity are two paramount traits in the engineering profession. Without

good intentions and truthfulness we would not have reliable trustworthy products. In the design,

there are different mechanical parts that are moving and rotating while the system is operating.

As engineers, there is an ethical and professional responsibility to ensure that nobody using the

product is prone to injury. There is also a need for accountability due to any damage caused by

the product. The pendulum design will not be released to the public for demonstration until the

system can be trusted to operate without risking the health of others. Another ethical responsibility that is related to safety is to only work in areas of understanding or competence.

Working in areas with little understanding is not efficient as well as not safe. It is a responsibility

of the team to educate and familiarize oneself with the topic that has been chosen to ensure that

the system is performing efficiently and safely.

## Safety:

Electrical
- E-Touch
- Capacitive sensor that detects when a user has provided a static charge or short circuit and will automatically turn off the power
Software
- Limits
- Designed to restrict the upper bounds of the provided commands and to make sure the acceleration and velocities don't exceed a maximum.
Mechanical
- Emergency Stop
- When pressed ON all electronics will have receive NO electric flow
- Protective Shield
- Shield designed to protect operators from pinch points created by the movement of the carriage along the rods
- Material of shield: Lexan or Acrylic
- Buzzer
- Designed to warn the operator when the system is in autonomous “swing up” mode using harmonic oscillations
- Power light
- The system will have an LED to indicate when it is receiving power
- TFT Screen
- The TFT screen will display what mode the system is currently running so the operator is aware.

## Impact Considerations:

- Due to the potential for collision, the capacitive e-stop and the manual e-stop will avoid

the severity of any damage. Also, keeping the pendulum longer will help reduce the needed

weight and acceleration of the carriage to limit the forces and torques produced in the pendulum

itself.

- The system will generate waste at the end of its life cycle. The goal is to minimize this

waste through the use of recyclable materials and COTS parts.


## References:

National Society of Professional Engineers. (2019, July). NSPE Code of Ethics for Engineers.

Nspe.org; National Society of Professional Engineers.

https://www.nspe.org/resources/ethics/code-ethics

## Appendix:

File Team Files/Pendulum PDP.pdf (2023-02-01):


# Inverted Pendulum PID Demonstrator

## Project Development Plan (PDP)

Matt Handley, Joseph Sedutto, Austin Cardosi, Kathryn Swineford

Southern New Hampshire University

Junior Engineering Design EG-310-20805 Spring 2023

February 1, 2023

# Roles

Team Member | Primary Role | Secondary Role
Matt Handley | CAD | Calculations
Joe Sedutto | Electrical | Machining
Kat Swineford | Documentation | Assembly
Austin Cardosi | Coding | File Organization

Table 1.1.1

SNHU, CETA | 2023, January

# Abstract

A PID loop (Proportional, Integral, Derivative) loop is a very common error-reducing

algorithm in our modern world. It can be implemented in many different ways, and controls

everything from the heating cycle of your toaster to the cruise control in your car.

The PID loop seeks to reduce the “error” in a system. That error may be the speed

you want to go, the target temperature of your toast or the upright position of a pendulum.

PIDs are used extensively in many different applications and can be difficult to understand on

a purely numeric basis. With that said, a PID demonstrator is a tool that allows users to

interact with and gain a deeper understanding of the underlying control mechanisms.

Out PID demonstrator tackles this problem, it uses robust but minimalist construction

to create a high quality and easy to maintain demonstrator. Users will interact with its front

panel to tune and de-tune a system managed by PID. We will use a classic inverted

pendulum which uses very similar principles to, balancing a baseball bat on your finger. Its

high moment of inertia allows the pendulum to swing and waver when untuned, yet hold

perfectly still when tuned correctly.

# Table of Contents

Roles | 2
Abstract | 3
Table of Contents | 4
Table of Figures | 5
Table of Tables | 5
The System Description | 7
Problem Statement | 7
Design Research | 7
Rotary Inverted Pendulum | 7
Reaction Wheel Inverted Pendulum | 8
Technical Challenges | 8
Customers/markets/economics/applications | 9
Concept of Operations | 9
Statements | 9
System Requirements (Top Level) | 12
Functional Requirements: (what it does) | 12
Performance Requirements: (how well it does) | 13
Physical Requirements: (sizes, weight) | 14
Environmental and Safety Requirements: | 14
Engineering Standards: | 15
Risk Assessments | 15
Risk Assessment | 15
Design Concepts | 17
Sketches | 17
System Composition Block Diagram | 19
Flow Chart of Operations | 20
Software Flow Chart | 21
Health and Safety Design Features: | 22
Used Engineering Standards: | 22
Task Plan | 23
Budget/BOM | 24
References | 25

Appendixes: | 26
Appendix A: Calculations / Model | 26
Appendix B: LibreOffice Schedule | 27

# Table of Figures

Figure 1.2.1 Rotary Inverted Pendulum | 6
Figure 1.2.2 Reaction Wheel Inverted Pendulum | 7
Figure 5.1.1 Blender Scale Model | 16
Figure 5.1.2 Blender Full Model | 16
Figure 5.1.3 Carriage Drawing | 16
Figure 5.1.4 Blender Motor Close-Up Model | 16
Figure 5.1.5 Belt Tensioning Cam Drawing | 17
Figure 5.1.6 Early Design Sketch | 17
Figure 6.1.1 System Composition Block Diagram | 17
Figure 6.2.1 Flow Chart of Operations | 18
Figure 6.3.1 Software Flowchart | 18
Figure 7.1.1 Task Plan | 23
Figure 8.1.1 Bill of Materials | 24
Figure 9.1.1 Calculations/Model | 26

# Table of Tables

Table 1.1.1 Team Roles | 2
Table 3.1.1 Functional Requirements | 12
Table 3.2.1 Performance Requirements | 12
Table 3.3.1 Physical Requirements | 13
Table 3.4.1 Environmental Requirements | 14
Table 3.5.1 Engineering Standards | 14

Table 4.1.1 Risk Assessment | 15

# The System Description

## Problem Statement

The goal is to make a PID Demonstrator that teaches the operator how to use a PID loop.

The operator will have control to adjust each individual variable and see how each effects a

vertical standing pendulum.

## Design Research

Rotary Inverted Pendulum

The rotary inverted pendulum spins about a fixed central axis. The arm that attaches

to the fixed central axis holds the pendulum. The combination of the motor and

sensors allow the pendulum to stand itself upright. Based on the pendulum's angle

the motor can accelerate in both directions to counterbalance the falling rod. The

assembly in Figure 1.2.1 below has an estimated cost of 200 to 500 dollars

depending on its final configuration.


(Figure: 1.2.1)

Reaction Wheel Inverted Pendulum

The Reaction Wheel inverted pendulum functions off torque by a spinning

wheel at the top of the pendulum. The torque and counter-torque used to move the

pendulum left or right can allow for the pendulum to have the ability to stand vertically

when the PID loop is corrected. This specific example was made with a variety of

Lego parts and the builder in the video we observed demonstrates that his loop works

with a variety of weights and modifications.

(Figure: 1.2.2)


Technical Challenges

One key challenge our team will face is trying to tune the pendulum to stay vertical as

the PID loop works to correct things according to the variables chosen. In order to

mitigate the above challenge the team will spend the right time perfecting the loop

after construction. Another challenge could be getting the pendulum to swing up

automatically without any outside assistance. A potential solution for this is to find

examples of this kind of pendulum and see how to possibly code a startup sequence.

Last potential challenge that might occur is troubleshooting the sensors to ensure accurate and precise readings for demonstrating the graphs of the PID loop. This can

be mitigated by testing the sensors prior to mounting them to the system.

## Customers/markets/economics/applications

Demonstrates control systems using a PID loop. Allows users to vary the control loop

constants to change the behavior of the pendulum. Educational application for academia and

industry.

# Concept of Operations
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

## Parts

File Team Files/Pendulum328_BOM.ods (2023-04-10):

Item | Qty | Reference(s) | Value | Price | Datasheet | Purchasing Link
1 | 1 | A101 | A4988 | $0.00 | https://www.pololu.com/product/2980/pictures
2 | 1 | C101 | 470uF | $0.00 | ~
3 | 1 | C102 | EYE_SP | $0.00 | https://github.com/adafruit/Adafruit-EYESPI-PCB
4 | 2 | C201, C202 | 100nf | $0.00 | ~
5 | 2 | C203, C204 | 22pf | $0.00 | ~
6 | 1 | C301 | 10uf | $0.00 | ~
7 | 6 | C302, C303, C401, C402, C403, C404 | 100nF | $0.00 | ~
8 | 1 | C304 | 1uF | $0.00 | ~
9 | 1 | D201 | STAT | $0.00 | ~
10 | 1 | D301 | PWR | $0.00 | ~
11 | 1 | D401 | RX | $0.00 | ~
12 | 1 | D402 | TX | $0.00 | ~
13 | 6 | H101, H102, H103, H104, H105, H106 | PiMountingHole | $0.00 | ~
14 | 1 | J101 | MOTOR | $0.00 | ~
15 | 1 | J102 | ENCODER | $0.00 | ~
16 | 1 | J201 | ICSP | $0.00 | ~
17 | 1 | J202 | Limit | $0.00 | ~
18 | 1 | J302 | 19V Input | $0.00 | ~
19 | 1 | J401 | USBC | $0.10 | https://www.usb.org/sites/default/files/documents/usb_type-c.zip
20 | 1 | J402 | PROG | $0.00 | ~
21 | 1 | JP101 | SolderJumper_2_Bridged | $0.00 | ~
22 | 1 | JP201 | RSTBridge | $0.00 | ~
23 | 1 | JP401 | SolderJumper_2_Open | $0.00 | ~
24 | 1 | Q101 | MMBT3904 | $0.00 | https://www.onsemi.com/pub/Collateral/2N3903-D.PDF
25 | 1 | Q102 | MMBT3906 | $0.00 | https://www.onsemi.com/pub/Collateral/2N3906-D.PDF
26 | 4 | R101, R207, R208, R402 | 10K | $0.00 | ~
27 | 1 | R102 | TBD | $0.00 | ~
28 | 7 | R201, R202, R203, R206, R301, R403, R404 | 1K | $0.00 | ~
29 | 1 | R401 | 4K7 | $0.00 | ~
30 | 2 | R405, R406 | 5K1 | $0.00 | ~
31 | 2 | R407, R408 | 22R | $0.00 | ~
32 | 1 | RV201 | P_Pot | $0.00 | ~
33 | 1 | RV202 | I_Pot | $0.00 | ~
34 | 1 | RV203 | D_Pot | $0.00 | ~
35 | 1 | SW201 | RESET | $0.00 | ~
36 | 1 | SW202 | START_SW | $0.00 | ~
37 | 1 | SW203 | STOP/MODE_SW | $0.00 | ~
38 | 2 | TP101, TP102 | TestPoint | $0.00 | ~
39 | 6 | TP103, TP104, TP105, TP106, TP107, TP108 | TestPoint | $0.00 | ~
40 | 1 | U201 | ATmega328P | $0.70 | http://ww1.microchip.com/downloads/en/DeviceDoc/ATmega328_P%20AVR%20MCU%20with%20picoPower%20Technology%20Data%20Sheet%2040001984A.pdf
41 | 1 | U301 | NCV1117ST50T3G | $0.50 | http://www.ti.com/lit/ds/symlink/lm1117.pdf
42 | 1 | U401 | FT232RL | $0.10 | https://www.ftdichip.com/Support/Documents/DataSheets/ICs/DS_FT232R.pdf
43 | 1 | Y201 | 16mHz | $0.01 | ~
44 | 1 | Carbon Fiber Tubing | 4ft | $19.94 |  | https://www.amazon.com/KARBXON-Carbon-1000mm-Lightweight-Strength/dp/B09QLGR7DB
45 | 4 | Linear Ball Bearing | 8mm | $7.99 |  | https://www.amazon.com/BELLA-BAYS-LM8UU-Bearings-Printer/dp/B08QGR2RZK
46 | 4 | Dry Bearings | 8mm | $6.99 |  | https://www.amazon.com/12PCs-Printer-Solid-Polymer-Bearing/dp/B076NK3GXG
47 | 1 | Timing Pulley |  | $16.23 |  | https://www.mcmaster.com/3764N105/
 |  |  | Total | $52.56

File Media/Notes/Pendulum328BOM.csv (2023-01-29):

Source: | /home/joe/git/SNHU/EG-310-InvertedPendulum/Hardware/PendulumController/PendulumController.kicad_sch
Date: | Mon 23 Jan 2023 03:47:49 PM EST
Tool: | Eeschema (6.0.9)
Generator: | /usr/share/kicad/plugins/bom_csv_grouped_by_value.py
Component Count: | 55
Collated Components:
Item | Qty | Reference(s) | Value | LibPart | Cost | Datasheet
1 | 1 | A101 | A4988 | Driver_Motor:Pololu_Breakout_A4988 | $1.99 | https://www.pololu.com/product/2980/pictures
2 | 1 | C101 | 10uf | Device:C_Polarized | $0.00 | ~
3 | 2 | C201, C202 | 100nf | Device:C_Small | $0.00 | ~
4 | 2 | C203, C204 | 22pf | Device:C_Small | $0.00 | ~
5 | 1 | C301 | 10uf | Device:C_Polarized_Small | $0.00 | ~
6 | 6 | C302, C303, C401, C402, C403, C404 | 100nF | Device:C_Small | $0.00 | ~
7 | 1 | C304 | 1uF | Device:C_Small | $0.00 | ~
8 | 1 | D101 | 1.8TFT | KenwoodFox:1.8TFT | $2.30
9 | 1 | D201 | STAT | Device:LED | $0.00 | ~
10 | 1 | D301 | PWR | Device:LED | $0.00 | ~
11 | 1 | D401 | RX | Device:LED | $0.00 | ~
12 | 1 | D402 | TX | Device:LED | $0.00 | ~
13 | 6 | H101, H102, H103, H104, H105, H106 | PiMountingHole | Mechanical:MountingHole | $0.00 | ~
14 | 1 | J101 | MOTOR | Connector:Conn_01x04_Male | $0.00 | ~
15 | 1 | J102 | ENCODER | Connector:Conn_01x04_Male | $0.00 | ~
16 | 1 | J201 | ICSP | Connector_Generic:Conn_02x05_Odd_Even | $0.00 | ~
17 | 1 | J301 | 19V Input | Connector:Barrel_Jack | $0.00 | ~
18 | 1 | J401 | USB_B_Micro | Connector:USB_B_Micro | $0.00 | ~
19 | 1 | J402 | PROG | Connector:Conn_01x06_Female | $0.00 | ~
20 | 1 | JP101 | SolderJumper_2_Bridged | Jumper:SolderJumper_2_Bridged | $0.00 | ~
21 | 1 | JP201 | RSTBridge | Jumper:SolderJumper_2_Bridged | $0.00 | ~
22 | 1 | JP401 | SolderJumper_2_Open | Jumper:SolderJumper_2_Open | $0.00 | ~
23 | 7 | R201, R202, R203, R206, R301, R403, R404 | 1K | Device:R_Small | $0.00 | ~
24 | 3 | R207, R208, R402 | 10K | Device:R_Small | $0.00 | ~
25 | 1 | R401 | 4K7 | Device:R_Small | $0.00 | ~
26 | 1 | RV201 | P_Pot | Device:R_Potentiometer | $0.00 | ~
27 | 1 | RV202 | I_Pot | Device:R_Potentiometer | $0.00 | ~
28 | 1 | RV203 | D_Pot | Device:R_Potentiometer | $0.00 | ~
29 | 1 | SW201 | RESET | Switch:SW_Push | $0.00 | ~
30 | 1 | SW202 | START_SW | Switch:SW_Push | $0.00 | ~
31 | 1 | SW203 | STOP/MODE_SW | Switch:SW_Push | $0.00 | ~
32 | 1 | U201 | ATmega328P | MCU_Microchip_ATmega:ATmega328P-A | $4.30 | http://ww1.microchip.com/downloads/en/DeviceDoc/ATmega328_P%20AVR%20MCU%20with%20picoPower%20Technology%20Data%20Sheet%2040001984A.pdf
33 | 1 | U301 | NCV1117ST50T3G | Regulator_Linear:LM1117-5.0 | $0.10 | http://www.ti.com/lit/ds/symlink/lm1117.pdf
34 | 1 | U401 | FT232RL | Interface_USB:FT232RL | $0.05 | https://www.ftdichip.com/Support/Documents/DataSheets/ICs/DS_FT232R.pdf
35 | 1 | Y201 | 16mHz | Device:Crystal | $0.00 | ~
36 | ? | N/A | 10ft Tube Stock Steel | N/A | $100.00
37 | ? | N/A | Wood Paneling | N/A | $35.00
38 | ? | N/A | 3D Printer Fillament | N/A | $10.00
39 | ? | N/A | Stepper Motor | N/A | $7.99
40 | ? | N/A | Bearings and Timing Belt | N/A | $20.00
41 | ? | N/A | Finishing Products | N/A | $15.00
42 | ? | N/A | Welding Gas and Consumables | N/A | $30.00
 |  |  |  |  | $226.73

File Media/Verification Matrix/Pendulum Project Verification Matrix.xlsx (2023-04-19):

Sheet: Ver_Matrix
 | Verification Matrix - Example
Requirement Type→ | Performance |  |  |  |  |  |  | Functional |  |  | Design |  |  |  |  |  |  |  | Interface |  |  | Resource |  | Verification Reference
Requirement Title→ | Self Tensioning | Low Power Mode | Autonomous Mode | User Control Mode | Mode Selection | Emergency Protection | TFT PID Constant Display | Require Power | Spin-Up in 20s | System Temp. | Span | Colored Interface | Frame Material | Pendulum Length | Factor of Safety | Fatigue Strength | Element Protection | Vibrations | Mechanical | Electrical | Software | Mass | Weight | This column identifies the specific verification summary related to the activity on each line. Multiple summaries may apply to a single line item.
Level of Assembly
System |  |  |  |  |  |  |  |  |  |  |  |  |  |  |  |  |  |  |  |  |  |  |  | Section 3.X Summaries
Frame Stability | IMT |  |  |  |  | AI |  |  |  |  |  |  |  |  | AT | AT | ATI | DIT | DIT |  |  |  | I | Section 3.5
Pendulum |  |  |  |  |  | IT |  |  |  |  |  |  |  | I |  |  |  |  | DT |  |  | I | I | Section 3.6
User Interactability and Legibility |  | DIT |  | DIT | DIT |  | DIT |  |  | MT |  | IT |  |  |  |  |  |  |  | IT | DIT |  |  | Section 3.2
Harmonic Oscilation |  |  |  |  |  |  |  |  | DITV |  |  |  |  |  |  |  |  |  |  | IT | DTV |  |  | Section 3.4
Autonomous Operation |  |  | DITV |  |  |  |  |  |  | MT |  |  |  |  |  |  |  |  |  | IT | DTV |  |  | Section 3.1
Subsystem/Assembly |  |  |  |  |  |  |  |  |  |  |  |  |  |  |  |  |  |  |  |  |  |  |  | Section 2.X Summaries
Frame Assembly | IMT |  |  |  |  |  |  |  |  |  | AIM |  | IT |  |  |  |  |  | DT |  |  |  |  | Section 2.6
Circuit Board |  | DTV | DT | DT | DIT | DIMT | I | IM |  | MT |  | IT |  |  |  |  |  |  |  | DIMT |  |  |  | Section 2.5
Sprocket and Belt Assembly | DT |  |  |  |  |  |  |  |  |  |  |  |  |  |  |  |  |  |  |  |  |  |  | Section 2.2
Belt Tensioning Assembly | DIT |  |  |  |  |  |  |  |  |  |  |  |  |  |  |  |  |  | DT |  |  |  |  | Section 2.1
User Interface |  | DT | DT | DT | DT |  | DITV |  |  |  |  | DIT |  |  |  |  |  |  | DT | IT |  |  |  | Section 2.7
Component |  |  |  |  |  |  |  |  |  |  |  |  |  |  |  |  |  |  |  |  |  |  |  | Section 1.X Summaries
Motors |  | DIT | DIT | DIT |  |  |  | MT | DIT |  |  |  |  |  |  |  |  |  | DIT | IT | DTV |  |  | Section 1.2
Encoder |  | DIT | DIT | DIT |  |  | ITV | MT | DIT |  |  |  |  |  |  |  |  |  |  | IT | DTV |  |  | Section 1.3
Limit Switches |  |  | DIT |  |  | DIT |  | MT |  |  |  |  |  |  |  |  |  |  |  | IT | IT |  |  | Section 1.4
Motor Controller |  | DIT | DIT | DIT |  |  |  | MT |  |  |  |  |  |  |  |  |  |  |  | IT | IT |  |  | Section 1.6
USB-C Port |  |  | T | T |  |  | IT | MT |  |  |  |  |  |  |  |  |  |  |  | IT | DTV |  |  | Section 1.7
Board Grounded |  | IM |  |  |  |  |  | IM |  |  |  |  |  |  |  |  |  |  |  |  |  |  |  | Section 1.8
Power Supply |  | IM |  |  |  | DIT |  | DMT |  | MT |  |  |  |  |  |  |  |  |  |  |  |  |  | Section 1.9
3 Potentiometers |  |  |  | DIT |  |  | ITV | MT |  |  |  |  |  |  |  |  |  |  |  | IT | DTV |  |  | Section 1.11
Estop |  |  |  |  |  | DIT |  | MT |  |  |  |  |  |  |  |  |  |  |  | DITV |  |  |  | Section 1.12
Power Switch |  |  |  |  |  |  |  | IT |  |  |  |  |  |  |  |  |  |  |  | DIT |  |  |  | Section 1.13
Toggle Button |  | DIT | DIT | DIT | DIT |  |  | MT |  |  |  |  |  |  |  |  |  |  |  | IT | DT |  |  | Section 1.14
Capacitive E-stop |  |  |  |  |  | DIT |  | MT |  |  |  |  |  |  |  |  |  |  |  | DITV |  |  |  | Section 1.15
TFT Screen |  |  |  | DITV |  |  |  | MT |  |  |  | IT |  |  |  |  |  |  |  | IT | DT |  |  | Section 1.16
Fan Cooling |  |  |  |  |  | MT |  | IMT |  | DMT |  |  |  |  |  |  |  |  |  | IT | DTV |  |  | Section 1.18
Verification Method: | Notes:
A - Analysis | 1. Color Scheme: Activities completed highlighted in GREEN; Activities to be completed highlighted in GOLD
D - Demonstration | 2. Summary References: Resolution (3.3.1), Frame Rate (3.3.2), Mechanical I/F (3.3.3), Electrical I/F (3.3.4), Mass (3.3.5), Power (3.3.6).
I - Inspection | 3. Support electronics used with camera assembly.
M - Measurement
T - Test
V - Validation of Records

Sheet: Example_1
 | Verification Matrix - Example
Requirement Type→ | Performance |  |  |  |  |  |  | Functional |  |  | Design |  |  |  |  |  |  |  | Interface |  |  | Resource |  | Verification Reference
Requirement Title→ | Self Tensioning | Low Power Mode | Autonomous Mode | User Control Mode | Mode Selection | Emergency Protection | TFT PID Constant Display | Require Power | Spin-Up in 20s | System Temp. | Span | Colored Interface | Frame Material | Pendulum Length | Factor of Safety | Fatigue Strength | Element Protection | Vibrations | Mechanical | Electrical | Software | Mass | Weight | This column identifies the specific verification summary related to the activity on each line. Multiple summaries may apply to a single line item.
Level of Assembly
System |  |  |  |  |  |  |  |  |  |  |  |  |  |  |  |  |  |  |  |  |  |  |  | Section 3.X Summaries
Frame Stability | IMT |  |  |  |  | AI |  |  |  |  |  |  |  |  | AT | AT | ATI | DIT | DIT |  |  |  | I | Section 3.5
Pendulum |  |  |  |  |  | IT |  |  |  |  |  |  |  | I |  |  |  |  | DT |  |  | I | I | Section 3.6
User Interactability and Legibility |  | DIT |  | DIT | DIT |  | DIT |  |  | MT |  | IT |  |  |  |  |  |  |  | IT | DIT |  |  | Section 3.2
Harmonic Oscilation |  |  |  |  |  |  |  |  | DITV |  |  |  |  |  |  |  |  |  |  | IT | DTV |  |  | Section 3.4
Autonomous Operation |  |  | DITV |  |  |  |  |  |  | MT |  |  |  |  |  |  |  |  |  | IT | DTV |  |  | Section 3.1
Subsystem/Assembly |  |  |  |  |  |  |  |  |  |  |  |  |  |  |  |  |  |  |  |  |  |  |  | Section 2.X Summaries
Frame Assembly | IMT |  |  |  |  |  |  |  |  |  | AIM |  | IT |  |  |  |  |  | DT |  |  |  |  | Section 2.6
Circuit Board |  | DTV | DT | DT | DIT | DIMT | I | IM |  | MT |  | IT |  |  |  |  |  |  |  | DIMT |  |  |  | Section 2.5
Sprocket and Belt Assembly | DT |  |  |  |  |  |  |  |  |  |  |  |  |  |  |  |  |  |  |  |  |  |  | Section 2.2
Belt Tensioning Assembly | DIT |  |  |  |  |  |  |  |  |  |  |  |  |  |  |  |  |  | DT |  |  |  |  | Section 2.1
User Interface |  | DT | DT | DT | DT |  | DITV |  |  |  |  | DIT |  |  |  |  |  |  | DT | IT |  |  |  | Section 2.7
Component |  |  |  |  |  |  |  |  |  |  |  |  |  |  |  |  |  |  |  |  |  |  |  | Section 1.X Summaries
Motors |  | DIT | DIT | DIT |  |  |  | MT | DIT |  |  |  |  |  |  |  |  |  | DIT | IT | DTV |  |  | Section 1.2
Encoder |  | DIT | DIT | DIT |  |  | ITV | MT | DIT |  |  |  |  |  |  |  |  |  |  | IT | DTV |  |  | Section 1.3
Limit Switches |  |  | DIT |  |  | DIT |  | MT |  |  |  |  |  |  |  |  |  |  |  | IT | IT |  |  | Section 1.4
Motor Controller |  | DIT | DIT | DIT |  |  |  | MT |  |  |  |  |  |  |  |  |  |  |  | IT | IT |  |  | Section 1.6
USB-C Port |  |  | T | T |  |  | IT | MT |  |  |  |  |  |  |  |  |  |  |  | IT | DTV |  |  | Section 1.7
Board Grounded |  | IM |  |  |  |  |  | IM |  |  |  |  |  |  |  |  |  |  |  |  |  |  |  | Section 1.8
Power Supply |  | IM |  |  |  | DIT |  | DMT |  | MT |  |  |  |  |  |  |  |  |  |  |  |  |  | Section 1.9
3 Potentiometers |  |  |  | DIT |  |  | ITV | MT |  |  |  |  |  |  |  |  |  |  |  | IT | DTV |  |  | Section 1.11
Estop |  |  |  |  |  | DIT |  | MT |  |  |  |  |  |  |  |  |  |  |  | DITV |  |  |  | Section 1.12
Power Switch |  |  |  |  |  |  |  | IT |  |  |  |  |  |  |  |  |  |  |  | DIT |  |  |  | Section 1.13
Toggle Button |  | DIT | DIT | DIT | DIT |  |  | MT |  |  |  |  |  |  |  |  |  |  |  | IT | DT |  |  | Section 1.14
Capacitive E-stop |  |  |  |  |  | DIT |  | MT |  |  |  |  |  |  |  |  |  |  |  | DITV |  |  |  | Section 1.15
TFT Screen |  |  |  | DITV |  |  |  | MT |  |  |  | IT |  |  |  |  |  |  |  | IT | DT |  |  | Section 1.16
Fan Cooling |  |  |  |  |  | MT |  | IMT |  | DMT |  |  |  |  |  |  |  |  |  | IT | DTV |  |  | Section 1.18
Verification Method: | Notes:
A - Analysis | 1. Color Scheme: Activities completed highlighted in GREEN; Activities to be completed highlighted in GOLD
D - Demonstration | 2. Summary References: Resolution (3.3.1), Frame Rate (3.3.2), Mechanical I/F (3.3.3), Electrical I/F (3.3.4), Mass (3.3.5), Power (3.3.6).
I - Inspection | 3. Support electronics used with camera assembly.
M - Measurement
T - Test
V - Validation of Records

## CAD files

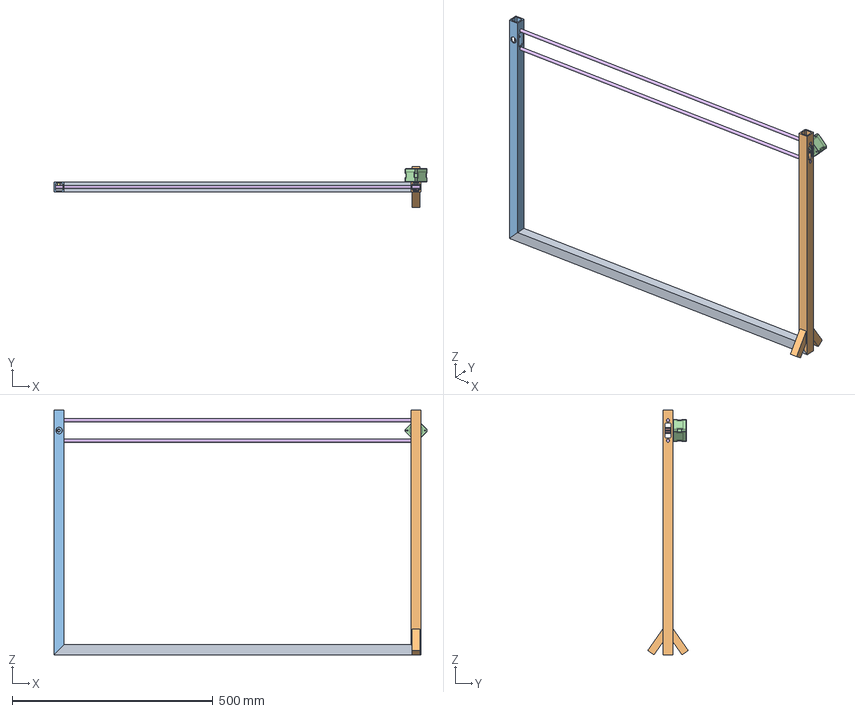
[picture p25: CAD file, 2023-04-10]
CAD/Components/FrameAssembly.step
928.9 x 101.1 x 609.6 mm
Lower Extrusion
Motor Extrusion
Endplate Extrusion
NEMA17
TimingPulley
Rail x 2
Eccentric

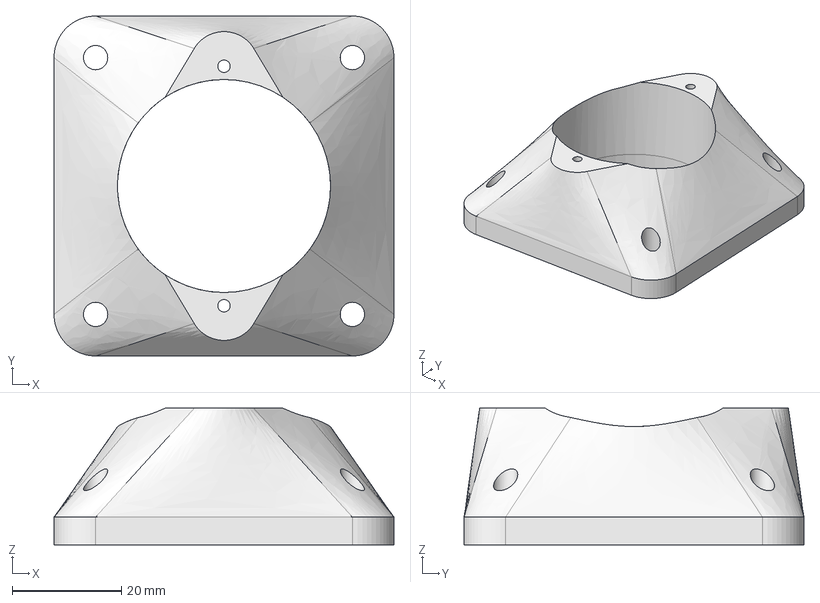
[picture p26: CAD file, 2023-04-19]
CAD/Components/NewMotorAdapter.FCStd
62.2 x 62.2 x 25.0 mm

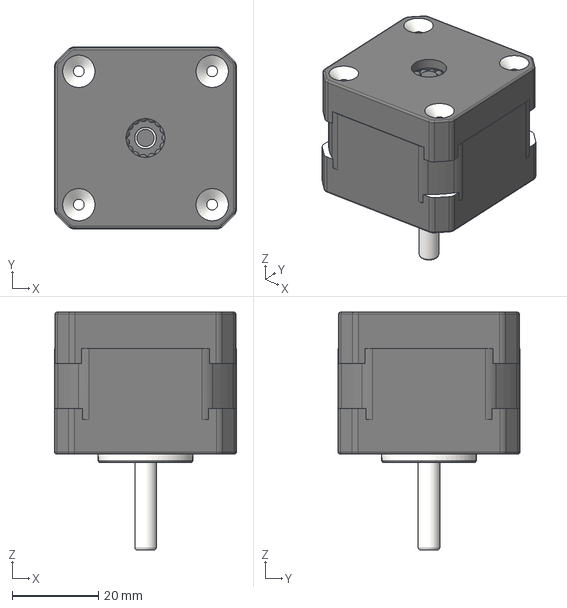
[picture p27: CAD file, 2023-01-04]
CAD/Resources/NEMA17.step
42.3 x 42.3 x 55.3 mm

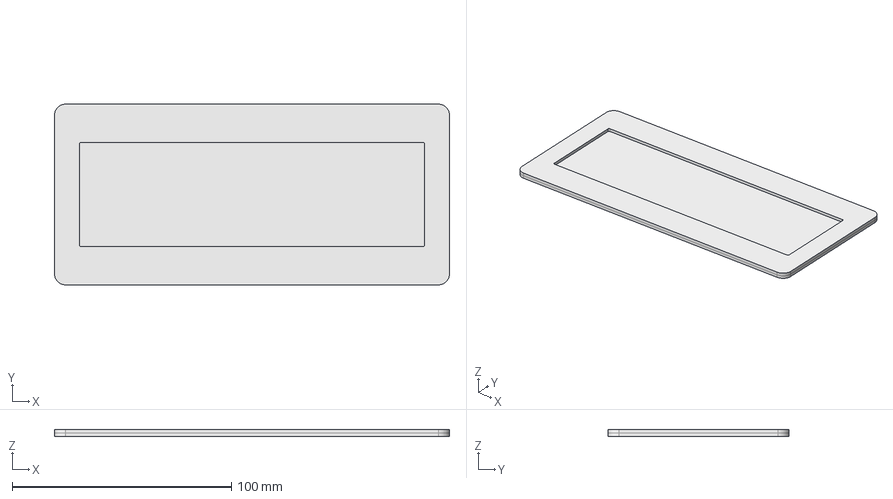
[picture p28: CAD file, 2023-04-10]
Hardware/Stencil.FCStd
180.3 x 82.6 x 3.17 mm

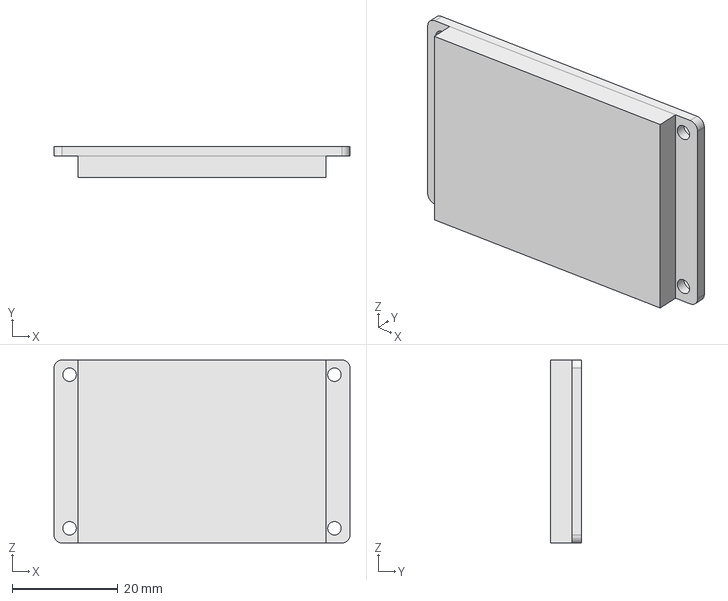
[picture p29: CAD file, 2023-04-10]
CAD/Components/Electronics.step
55.9 x 5.84 x 34.5 mm

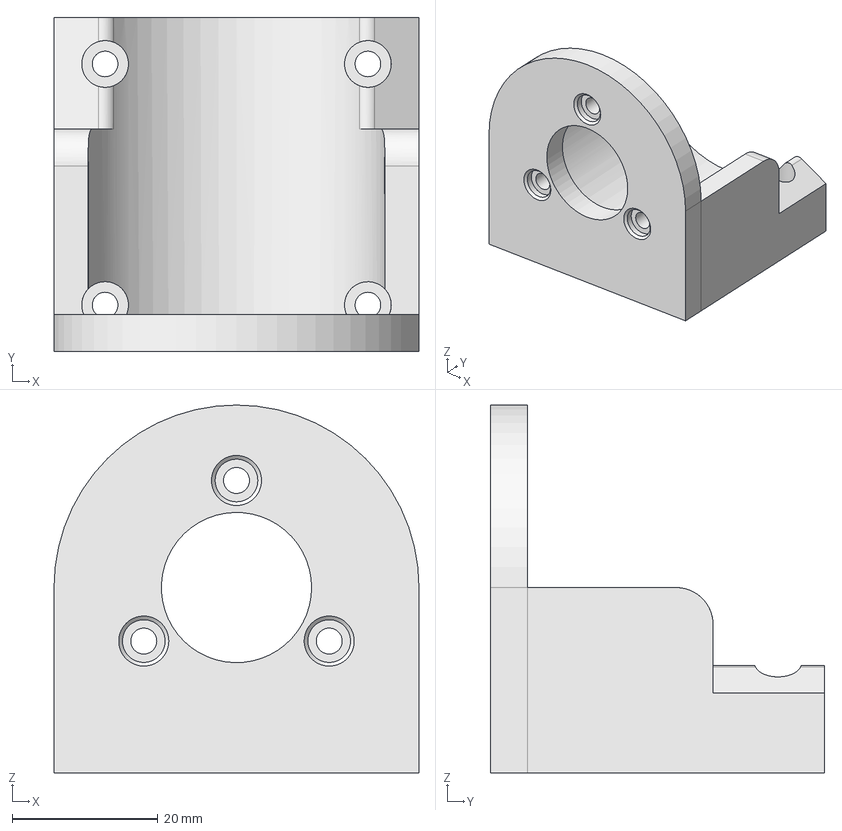
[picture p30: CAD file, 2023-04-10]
CAD/Components/Frame.FCStd
50.0 x 45.7 x 50.4 mm

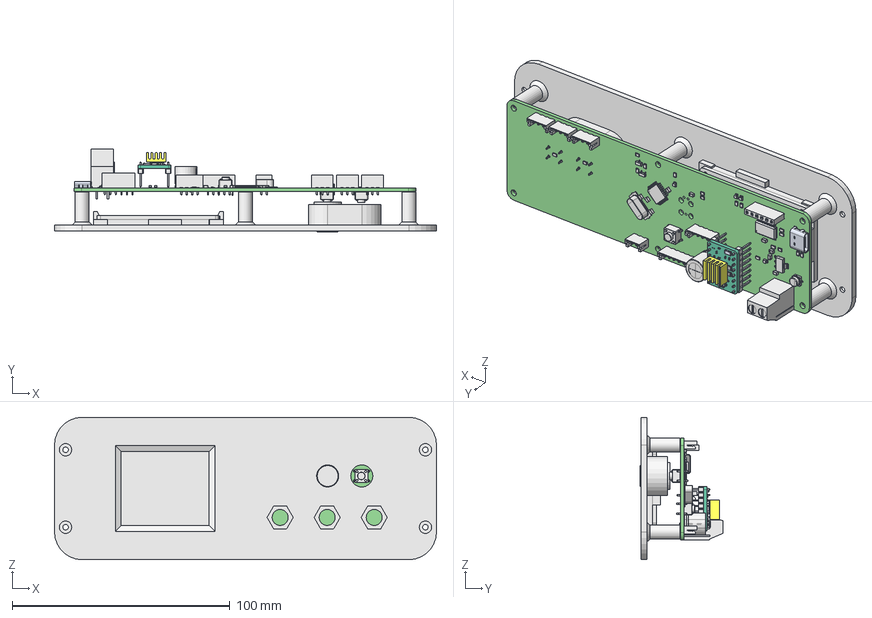
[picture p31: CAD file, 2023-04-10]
CAD/Components/ElectronicsAndBezel.FCStd
175.4 x 38.2 x 65.4 mm
Screen
Bezel
tmpslifkoxg PCB
PushButton

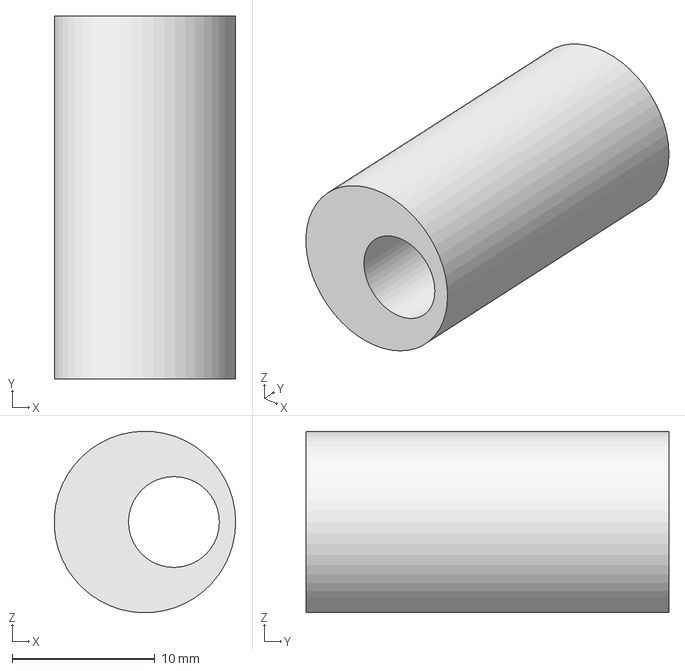
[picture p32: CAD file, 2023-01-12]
CAD/Components/TempCam.FCStd
12.7 x 25.4 x 12.7 mm

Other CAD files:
CAD/Matt's CDR CAD Files (Inventor Professional Format)/Drawings/Different Carriage Type Exploded Drawings/Carriage Type 2 Assembly V1 Exploded View.dwg
CAD/Matt's CDR CAD Files (Inventor Professional Format)/Drawings/Full Assembly Exploded View and Parts List V1.dwg
CAD/Matt's CDR CAD Files (Inventor Professional Format)/Drawings/Different Carriage Type Exploded Drawings/Carriage Type 1 Assembly V1 Exploded View.dwg
CAD/Cosmetic/Badge.blend
CAD/Frame Pieces/Eccentric.ipt
CAD/Frame Pieces/Endplate Extrusion.ipt
CAD/Frame Pieces/Lower Extrusion.ipt
CAD/Frame Pieces/Motor Extrusion.ipt
CAD/Frame Pieces/NEMA17.ipt
CAD/Frame Pieces/Rail.ipt
CAD/Frame Pieces/TimingPulley.ipt
CAD/Matt's CDR CAD Files (Inventor Professional Format)/Assemblies/Carriage Assemblies/Carriage Type 1 V1 Assembly.iam
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

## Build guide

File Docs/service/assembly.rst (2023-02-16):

Assembly
========

The Pendulum 328 is a prototype built from prototype parts with the primary goal of
being an educational tool.

Should parts ever need to be re-ordered, or this process used to drive future projects,
this section of the documentation details those processes!

Ordering the PCB
----------------

The Pendulum 328's CI/CD will automatically attach new builds of the gerber files to each release,
when ordering new boards, always use the release tagged Latest_. (Not necessarily the release in the photo.)

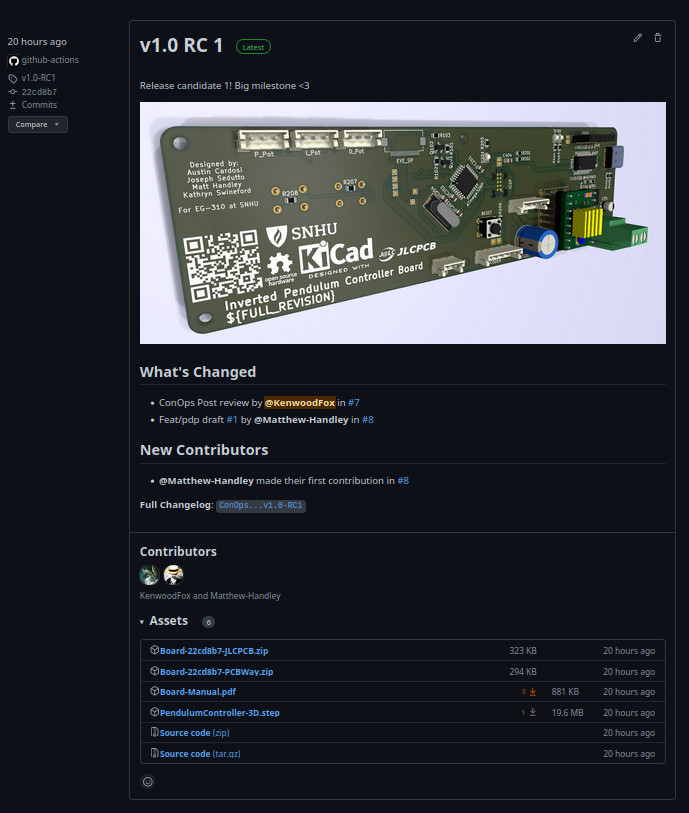
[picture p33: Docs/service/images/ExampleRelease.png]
An example of a release


This guide will use JLCPCB_ for ordering the boards, but we also build gerbers for PCBWay_ as well.

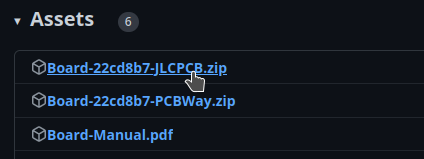
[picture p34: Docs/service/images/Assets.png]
Assets


From the assets section at the bottom of the release, there should be two or more gerber zip files with each
fab's name and the **Commit Hash** for this build. Download the appropriate one for your fab. (In this case, JLCPCB_)

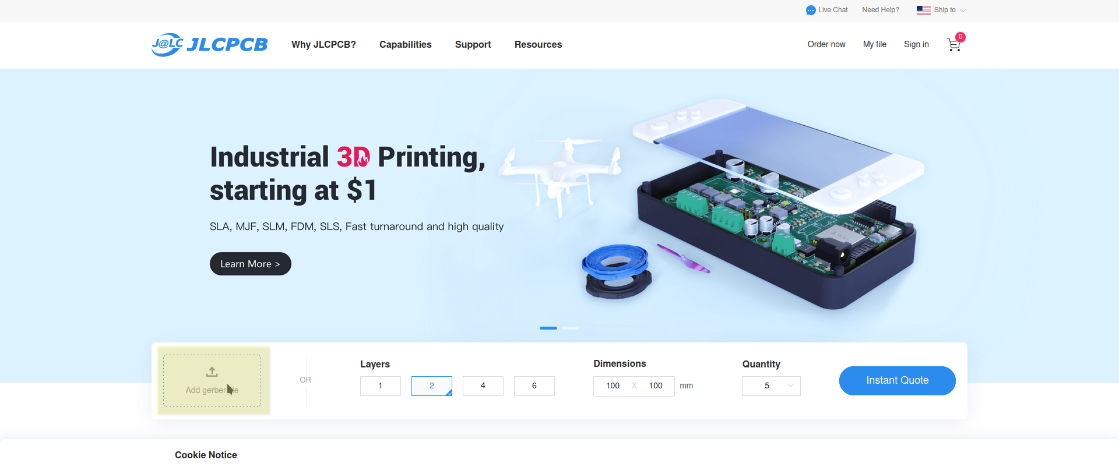
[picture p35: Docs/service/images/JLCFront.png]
JLC Front Page


Right on the front page there is a box to upload your gerber .zip file. JLC will take you to the ordering and qouting page.

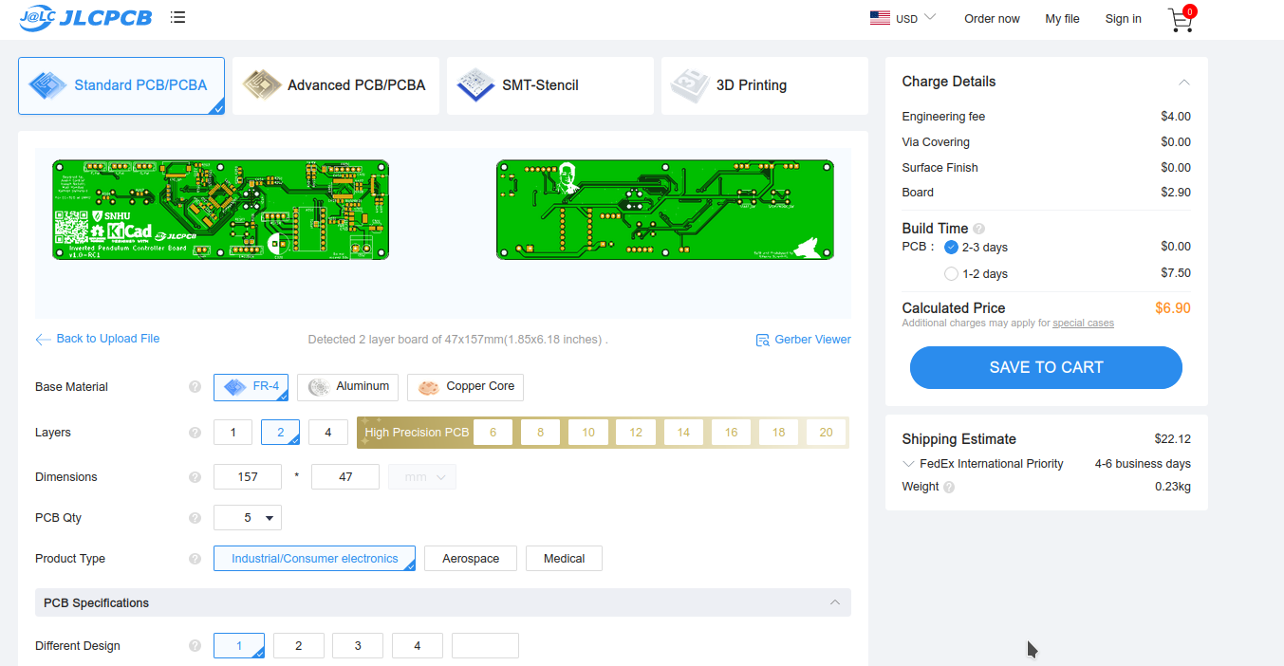
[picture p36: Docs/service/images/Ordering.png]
JLC Ordering Page


There are a few important settings we **MUST** change here.

Scroll to the bottom of the ordering page and find the stencil section.

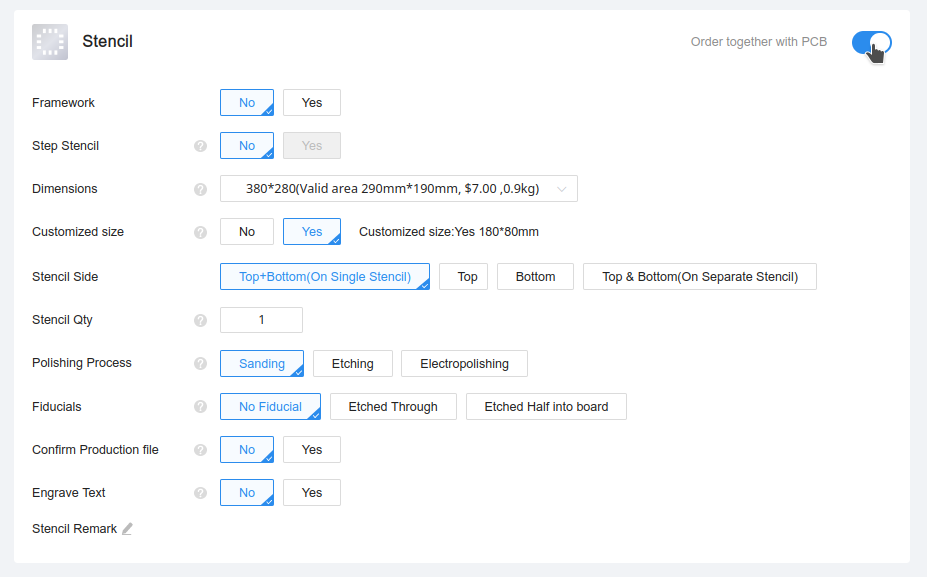
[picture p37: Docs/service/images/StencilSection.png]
JLC Stencil Section


This board uses SMD components and requires a stencil.

To save on cost and reduce shipping time, the stencil size must be modified, after **checking the toggle**
to enable the stencil, find and click the **Customized size** button, and input `180mmx80mm`.

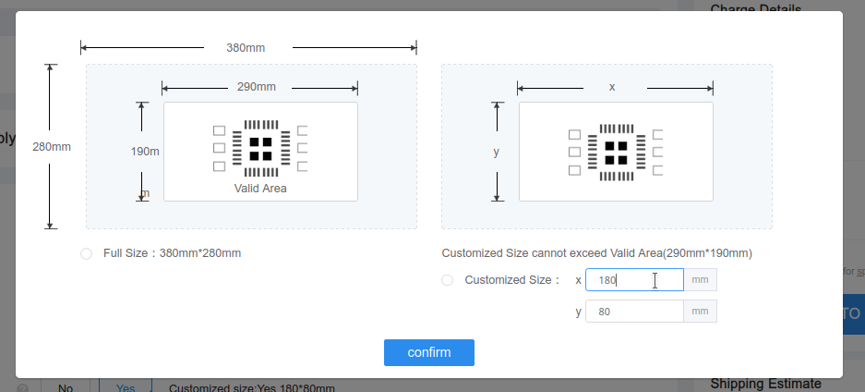
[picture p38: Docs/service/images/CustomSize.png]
JLC Stencil Define


This stencil size is perfectly adequate the cover the board, and can be found within the `User.Drawings`
layer in KiCAD.

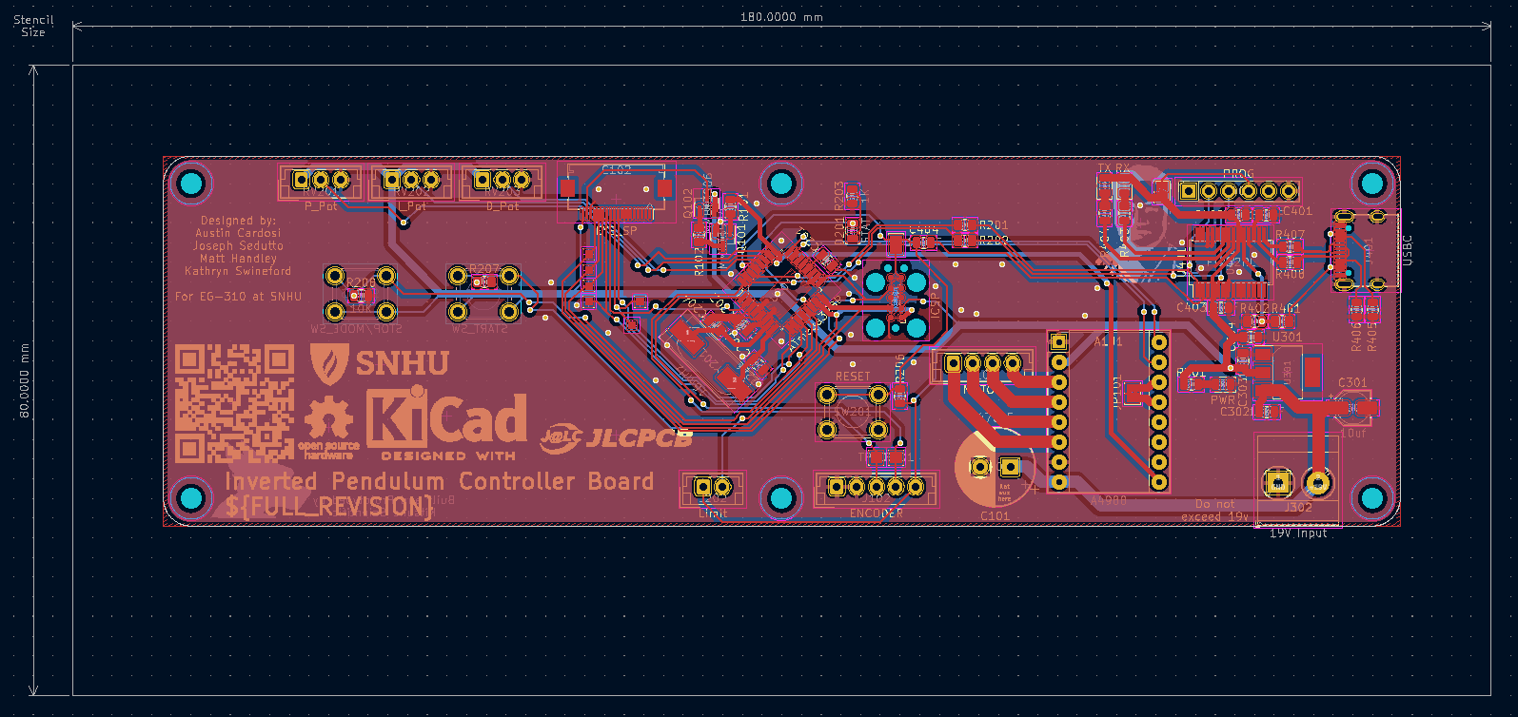
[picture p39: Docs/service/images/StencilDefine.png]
Kicad Stencil Define


All Other defaults should be acceptable, and at the end the order should look something like this:

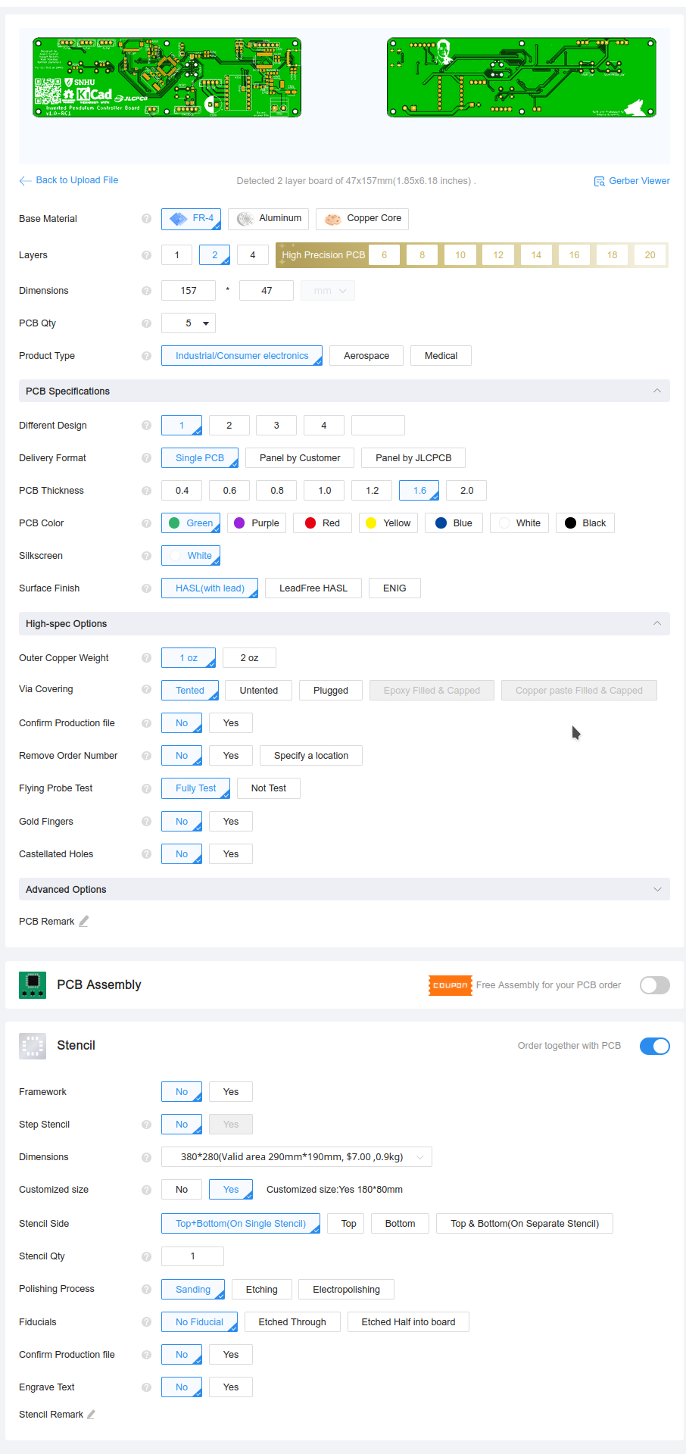
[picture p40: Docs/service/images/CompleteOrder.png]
Complete Order


Good luck!

.. _Latest: https://github.com/KenwoodFox/EG-310-InvertedPendulum/releases/latest
.. _JLCPCB: https://jlcpcb.com/
.. _PCBWay: https://www.pcbway.com/

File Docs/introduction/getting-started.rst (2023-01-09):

Getting Started
===============

Introduction
------------

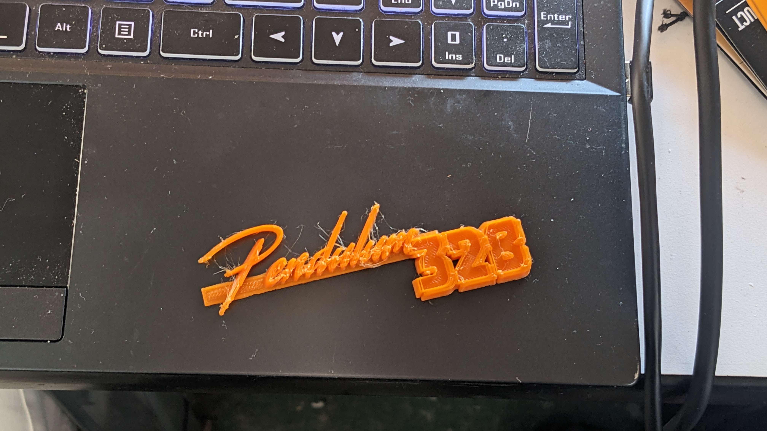
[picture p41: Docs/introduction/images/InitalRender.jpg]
Initial Render


Welcome! This section is yet to be filled out.

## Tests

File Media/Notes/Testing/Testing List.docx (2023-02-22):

Testing

Pendulum-328

2/6/23

Test 1: Bearing

Use different bearings to see how they move/operate within the system.

Test 2: Pendulum length/weight

Use various pendulum lengths/weights to determine the most appropriate length/weight that works for our system.

Test 3: Legs

Use different attachable legs to determine whether the system operates better with or without legs. As well as determining what material works best for the legs.

Test 4: Motors

Use a motor and measure the different properties such as electrical load as well as seeing if the motor overheats.

Test 5: Velocities

Use different velocities to decide what velocity is most appropriate for the system.

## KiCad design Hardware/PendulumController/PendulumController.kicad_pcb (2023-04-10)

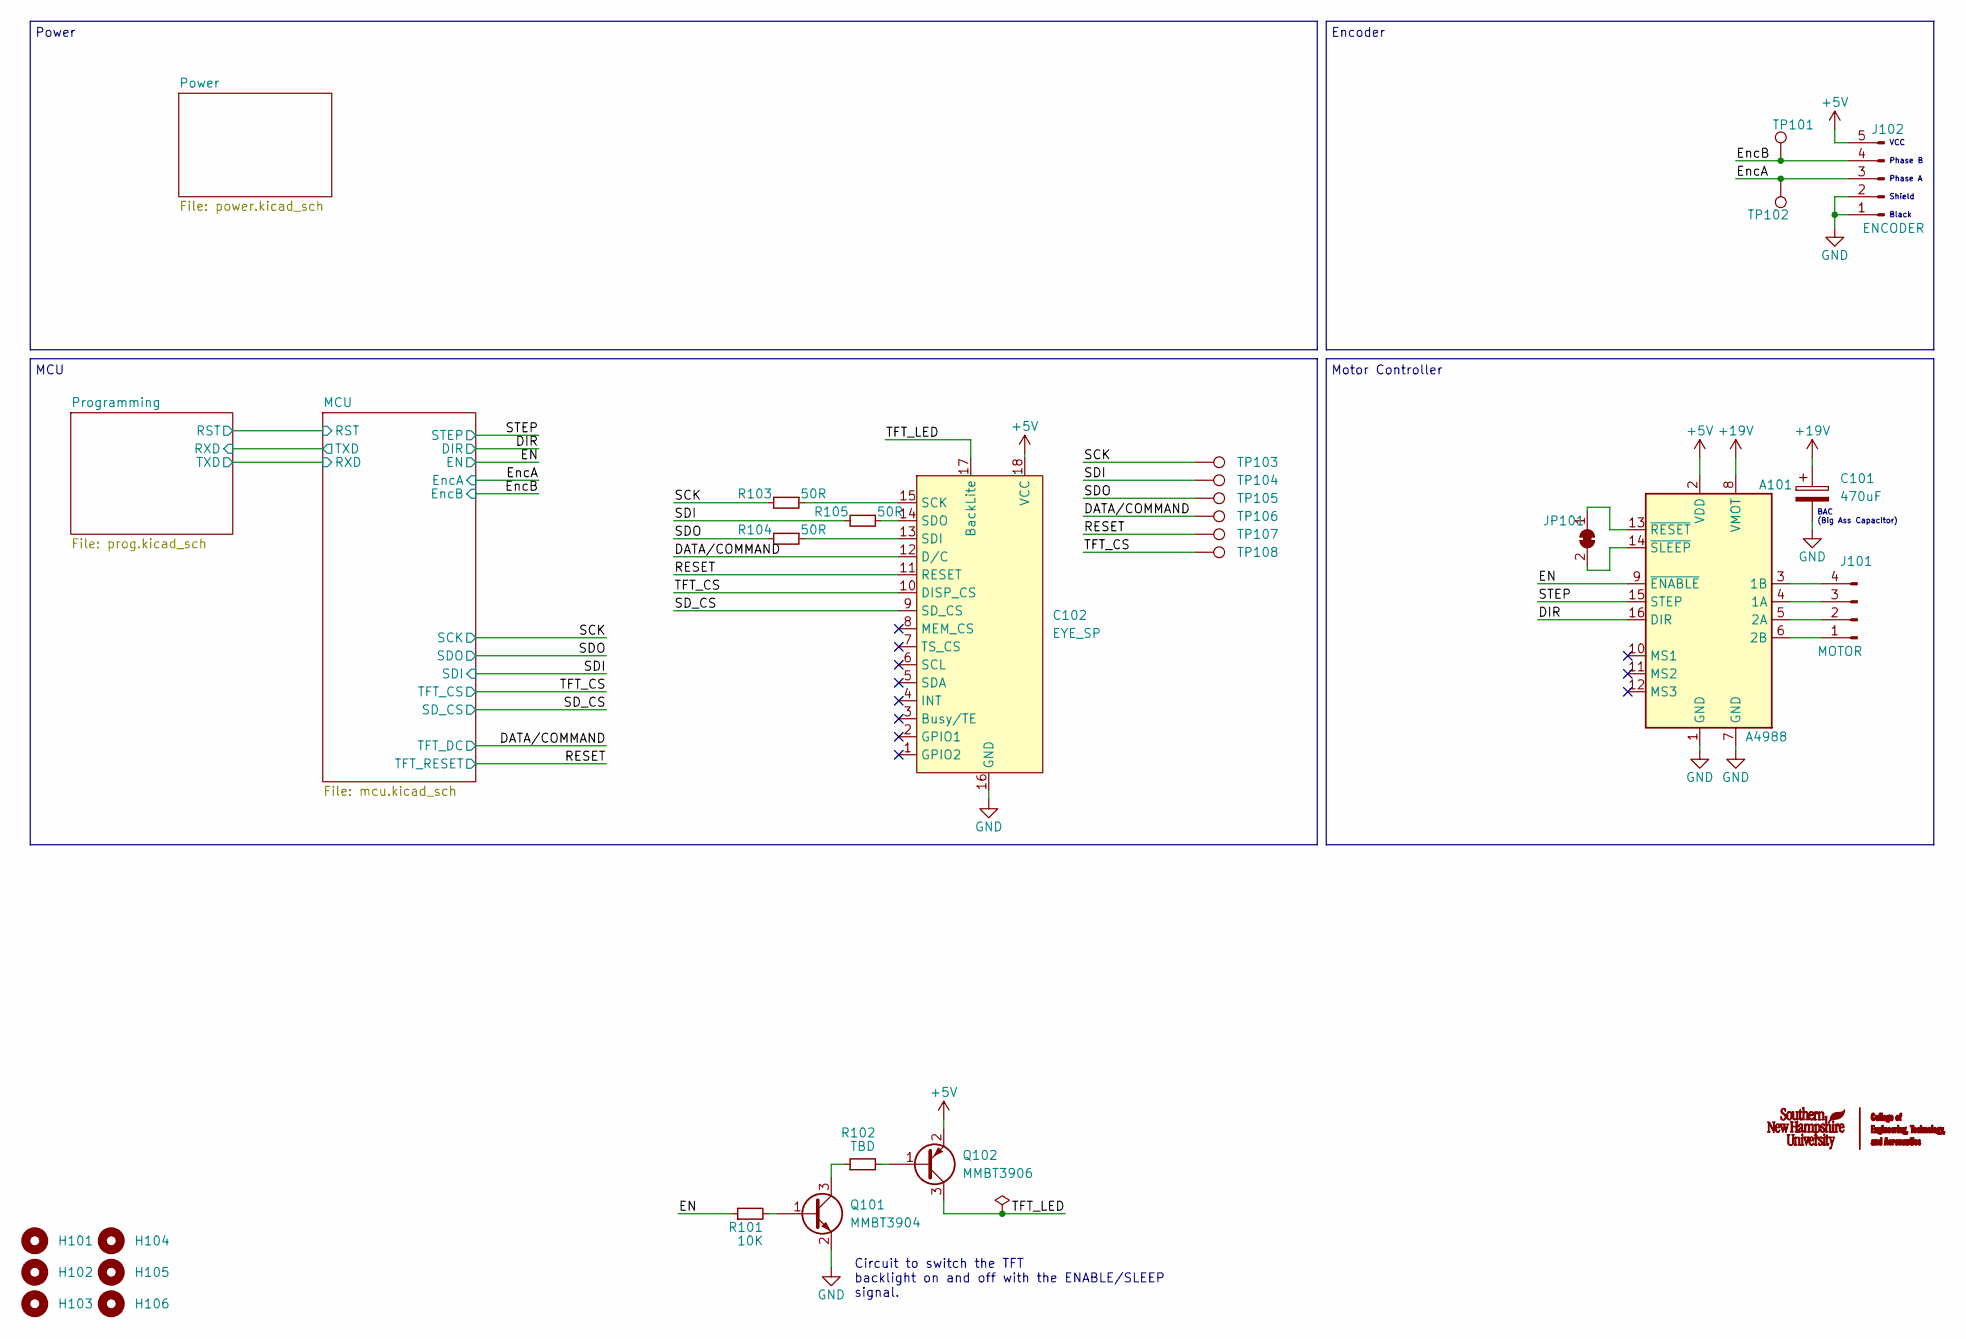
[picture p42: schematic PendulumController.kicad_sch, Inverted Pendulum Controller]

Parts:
A101: A4988; Pololu_Breakout-16_15.2x20.3mm
C101: 470uF; CP_Radial_D10.0mm_P3.80mm
C102: EYE_SP; Hirose_FH12-18S-0.5SH_1x18-1MP_P0.50mm_Horizontal
H101, H102, H103, H104, H105, H106: PiMountingHole; MountingHole_2.7mm
J101: MOTOR; JST_EH_B4B-EH-A_1x04_P2.50mm_Vertical
J102: ENCODER; JST_EH_B5B-EH-A_1x05_P2.50mm_Vertical
JP101: SolderJumper_2_Bridged; SolderJumper-2_P1.3mm_Bridged2Bar_Pad1.0x1.5mm
Q101: MMBT3904; SOT-23
Q102: MMBT3906; SOT-23
R101: 10K; R_0805_2012Metric
R102: TBD; R_0805_2012Metric
R103, R104, R105: 50R; R_0805_2012Metric
TP101, TP102: TestPoint; TestPoint_Pad_1.5x1.5mm
TP103, TP104, TP105, TP106, TP107, TP108: TestPoint; TestPoint_Pad_1.0x1.0mm

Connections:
+5V: A101.2 (VDD), C102.18 (VCC), J102.5, Q102.2 (E); also elsewhere on the board
+19V: A101.8 (VMOT), C101.1; also elsewhere on the board
/DATA/COMMAND: C102.12 (D/C), TP106.1; also elsewhere on the board
/DIR: A101.16 (DIR); also elsewhere on the board
/EN: A101.9 (~ENABLE), R101.1; also elsewhere on the board
/EncA: J102.3, TP102.1; also elsewhere on the board
/EncB: J102.4, TP101.1; also elsewhere on the board
/RESET: C102.11 (RESET), TP107.1; also elsewhere on the board
/SCK: R103.2, TP103.1; also elsewhere on the board
/SDI: R105.2, TP104.1; also elsewhere on the board
/SDO: R104.2, TP105.1; also elsewhere on the board
/SD_CS: C102.9 (SD_CS); also elsewhere on the board
/STEP: A101.15 (STEP); also elsewhere on the board
/TFT_CS: C102.10 (DISP_CS), TP108.1; also elsewhere on the board
/TFT_LED: C102.17 (BackLite), Q102.3 (C)
GND: A101.1 (GND), A101.7 (GND), C101.2, C102.16 (GND), J102.1, J102.2, Q101.2 (E); also elsewhere on the board
unnamed: A101.3 (1B), J101.4
unnamed: A101.4 (1A), J101.3
unnamed: A101.5 (2A), J101.2
unnamed: A101.6 (2B), J101.1
unnamed: A101.13 (~RESET), JP101.1 (A)
unnamed: A101.14 (~SLEEP), JP101.2 (B)
unnamed: C102.13 (SDI), R104.1
unnamed: C102.14 (SDO), R105.1
unnamed: C102.15 (SCK), R103.1
unnamed: Q101.1 (B), R101.2
unnamed: Q101.3 (C), R102.1
unnamed: Q102.1 (B), R102.2

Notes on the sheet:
Shield
Phase B
Power
Encoder
MCU
Circuit to switch the TFT backlight on and off with the ENABLE/SLEEP signal.
Black
BAC (Big Ass Capacitor)
Phase A
Motor Controller
VCC

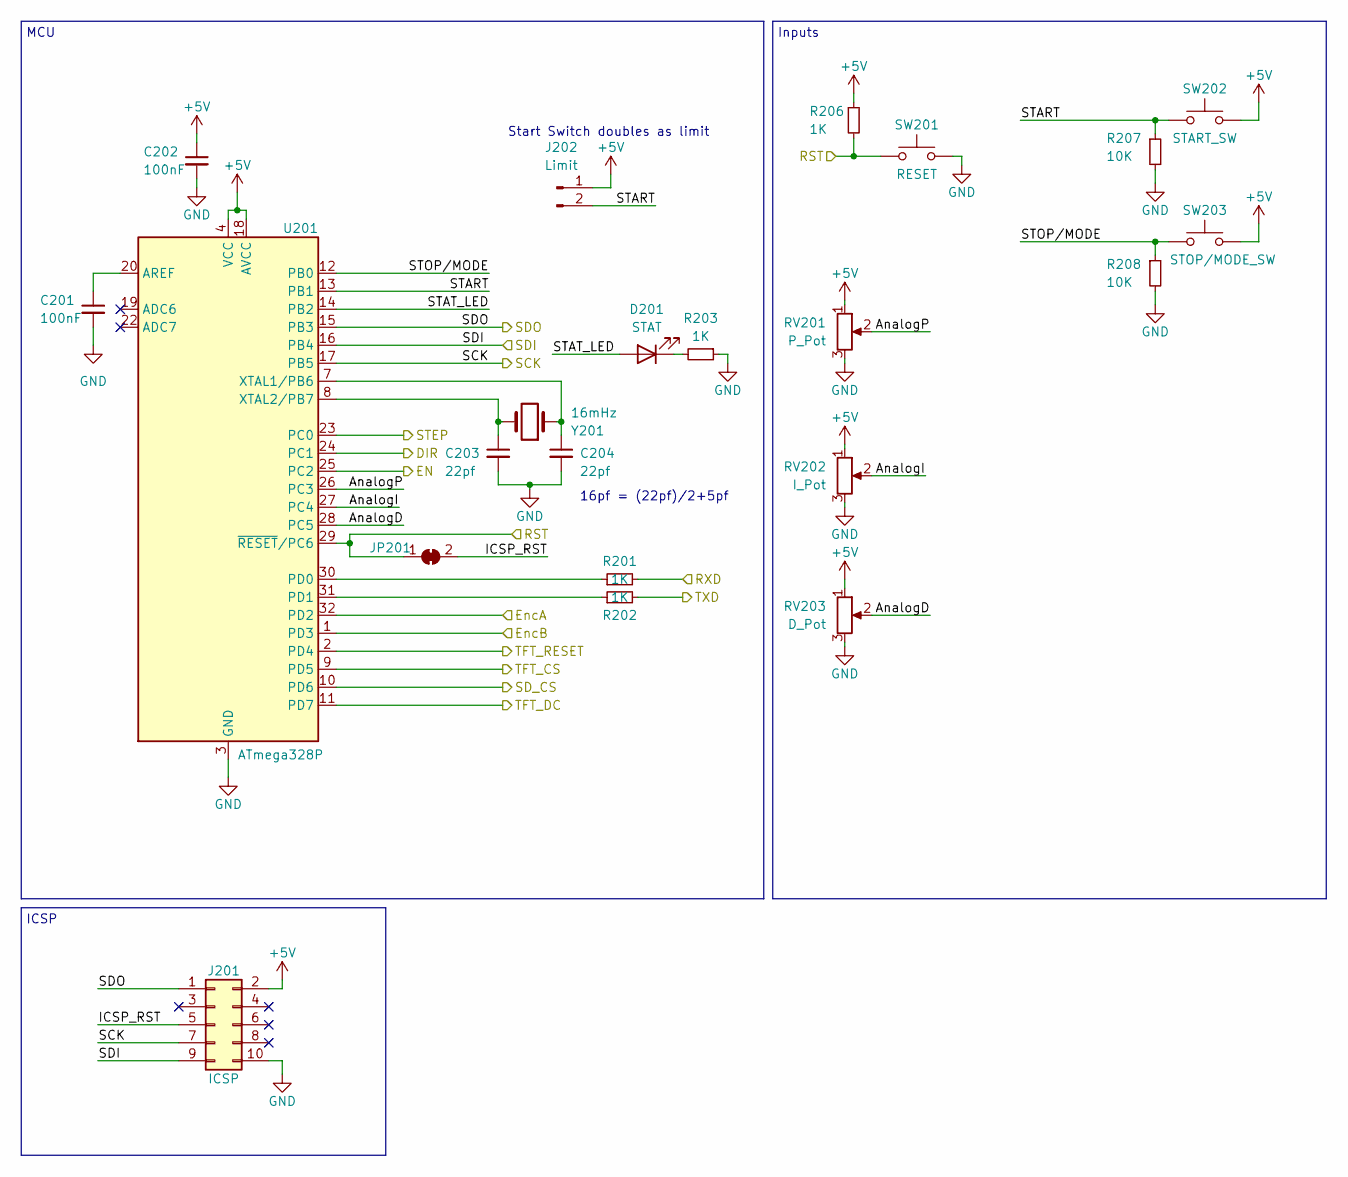
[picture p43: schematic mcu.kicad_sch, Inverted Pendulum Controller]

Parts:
C201, C202: 100nF; C_0805_2012Metric
C203, C204: 22pf; C_0805_2012Metric
D201: STAT; LED_0805_2012Metric
J201: ICSP; Tag-Connect_TC2050-IDC-FP_2x05_P1.27mm_Vertical
J202: Limit; JST_EH_B2B-EH-A_1x02_P2.50mm_Vertical
JP201: RSTBridge; SolderJumper-2_P1.3mm_Bridged_Pad1.0x1.5mm
R201, R202, R203, R206: 1K; R_0805_2012Metric
R207, R208: 10K; R_0805_2012Metric
RV201: P_Pot; JST_EH_B3B-EH-A_1x03_P2.50mm_Vertical
RV202: I_Pot; JST_EH_B3B-EH-A_1x03_P2.50mm_Vertical
RV203: D_Pot; JST_EH_B3B-EH-A_1x03_P2.50mm_Vertical
SW201: RESET; SW_PUSH_6mm_H5mm
SW202: START_SW; SW_PUSH_6mm_H5mm
SW203: STOP/MODE_SW; SW_PUSH_6mm_H5mm
U201: ATmega328P; TQFP-32_7x7mm_P0.8mm
Y201: 16mHz; Crystal_SMD_HC49-SD

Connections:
+5V: C202.1, J201.2, J202.1, R206.1, RV201.1, RV202.1, RV203.1, SW202.2, SW203.2, U201.4 (VCC), U201.6 (VCC), U201.18 (AVCC); also elsewhere on the board
/DATA/COMMAND: U201.11 (PD7); also elsewhere on the board
/DIR: U201.24 (PC1); also elsewhere on the board
/EN: U201.25 (PC2); also elsewhere on the board
/EncA: U201.32 (PD2); also elsewhere on the board
/EncB: U201.1 (PD3); also elsewhere on the board
/MCU/AnalogD: RV203.2, U201.28 (PC5)
/MCU/AnalogI: RV202.2, U201.27 (PC4)
/MCU/AnalogP: RV201.2, U201.26 (PC3)
/MCU/ICSP_RST: J201.5, JP201.2 (B)
/MCU/RST: JP201.1 (A), R206.2, SW201.1, U201.29 (~RESET/PC6); also elsewhere on the board
/MCU/RXD: R201.2; also elsewhere on the board
/MCU/START: J202.2, R207.1, SW202.1, U201.13 (PB1)
/MCU/STAT_LED: D201.2 (A), U201.14 (PB2)
/MCU/STOP/MODE: R208.1, SW203.1, U201.12 (PB0)
/MCU/TXD: R202.2; also elsewhere on the board
/RESET: U201.2 (PD4); also elsewhere on the board
/SCK: J201.7, U201.17 (PB5); also elsewhere on the board
/SDI: J201.9, U201.16 (PB4); also elsewhere on the board
/SDO: J201.1, U201.15 (PB3); also elsewhere on the board
/SD_CS: U201.10 (PD6); also elsewhere on the board
/STEP: U201.23 (PC0); also elsewhere on the board
/TFT_CS: U201.9 (PD5); also elsewhere on the board
GND: C201.2, C202.2, C203.2, C204.2, J201.10, R203.1, R207.2, R208.2, RV201.3, RV202.3, RV203.3, SW201.2, U201.3 (GND), U201.5 (GND), U201.21 (GND); also elsewhere on the board
unnamed: C201.1, U201.20 (AREF)
unnamed: C203.1, U201.8 (XTAL2/PB7), Y201.2
unnamed: C204.1, U201.7 (XTAL1/PB6), Y201.1
unnamed: D201.1 (K), R203.2
unnamed: R201.1, U201.30 (PD0)
unnamed: R202.1, U201.31 (PD1)

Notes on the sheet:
ICSP
Start Switch doubles as limit
MCU
Inputs
16pf = (22pf)/2+5pf

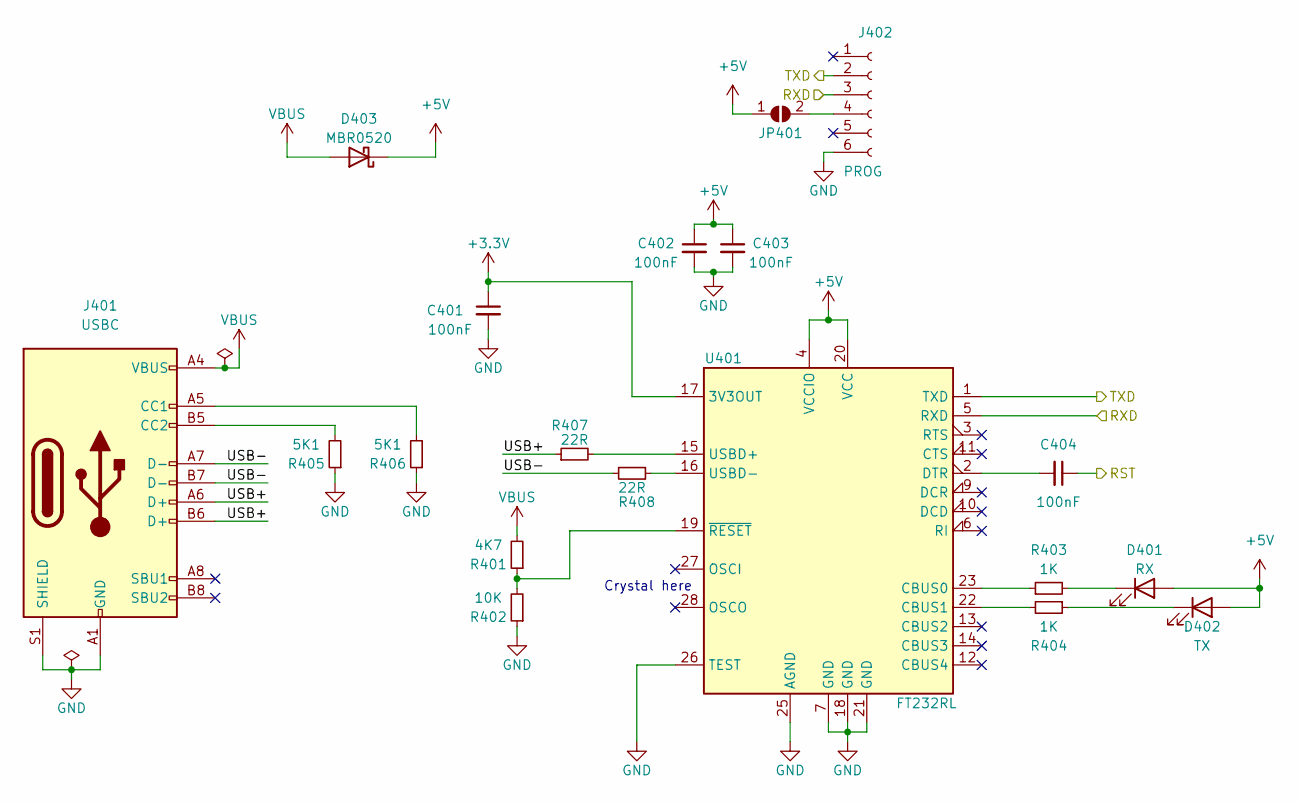
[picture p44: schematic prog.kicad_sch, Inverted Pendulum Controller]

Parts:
C401, C402, C403, C404: 100nF; C_0805_2012Metric
D401: RX; LED_0805_2012Metric
D402: TX; LED_0805_2012Metric
D403: MBR0520; D_SOD-123
J401: USBC; USB_C_Receptacle_XKB_U262-16XN-4BVC11
J402: PROG; PinSocket_1x06_P2.54mm_Vertical
JP401: SolderJumper_2_Open; SolderJumper-2_P1.3mm_Open_TrianglePad1.0x1.5mm
R401: 4K7; R_0805_2012Metric
R402: 10K; R_0805_2012Metric
R403, R404: 1K; R_0805_2012Metric
R405, R406: 5K1; R_0805_2012Metric
R407, R408: 22R; R_0805_2012Metric
U401: FT232RL; SSOP-28_5.3x10.2mm_P0.65mm

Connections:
+3.3V: C401.1, U401.17 (3V3OUT)
+5V: C402.1, C403.1, D401.2 (A), D402.2 (A), D403.1 (K), JP401.1 (A), U401.4 (VCCIO), U401.20 (VCC); also elsewhere on the board
/MCU/RST: C404.1; also elsewhere on the board
/MCU/RXD: J402.2, U401.1 (TXD); also elsewhere on the board
/MCU/TXD: J402.3, U401.5 (RXD); also elsewhere on the board
/Programming/USB+: J401.A6 (D+), J401.B6 (D+), R407.1
/Programming/USB-: J401.A7 (D-), J401.B7 (D-), R408.2
GND: C401.2, C402.2, C403.2, J401.A1 (GND), J401.A12 (GND), J401.B1 (GND), J401.B12 (GND), J401.S1 (SHIELD), J402.6, R402.1, R405.1, R406.1, U401.7 (GND), U401.18 (GND), U401.21 (GND), U401.25 (AGND), U401.26 (TEST); also elsewhere on the board
unnamed: C404.2, U401.2 (DTR)
unnamed: D401.1 (K), R403.2
unnamed: D402.1 (K), R404.1
unnamed: J401.A5 (CC1), R406.2
unnamed: J401.B5 (CC2), R405.2
unnamed: J402.4, JP401.2 (B)
unnamed: R401.1, R402.2, U401.19 (~RESET)
unnamed: R403.1, U401.23 (CBUS0)
unnamed: R404.2, U401.22 (CBUS1)
unnamed: R407.2, U401.15 (USBD+)
unnamed: R408.1, U401.16 (USBD-)
VBUS: D403.2 (A), J401.A4 (VBUS), J401.A9 (VBUS), J401.B4 (VBUS), J401.B9 (VBUS), R401.2

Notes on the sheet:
Crystal here

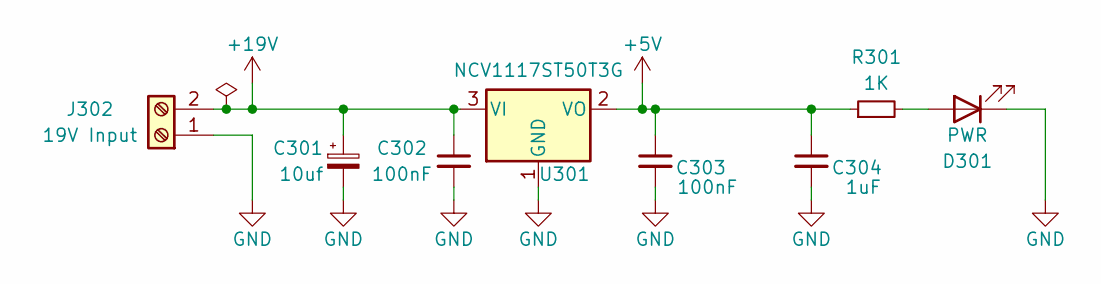
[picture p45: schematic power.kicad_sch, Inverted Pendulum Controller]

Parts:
C301: 10uf; CP_Elec_4x3
C302, C303: 100nF; C_0805_2012Metric
C304: 1uF; C_0805_2012Metric
D301: PWR; LED_0805_2012Metric
J302: 19V Input; TerminalBlock_Phoenix_MKDS-3-2-5.08_1x02_P5.08mm_Horizontal
R301: 1K; R_0805_2012Metric
U301: NCV1117ST50T3G; SOT-223

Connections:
+5V: C303.1, C304.1, R301.1, U301.2 (VO); also elsewhere on the board
+19V: C301.1, C302.1, J302.2, U301.3 (VI); also elsewhere on the board
GND: C301.2, C302.2, C303.2, C304.2, D301.1 (K), J302.1, U301.1 (GND); also elsewhere on the board
unnamed: D301.2 (A), R301.2

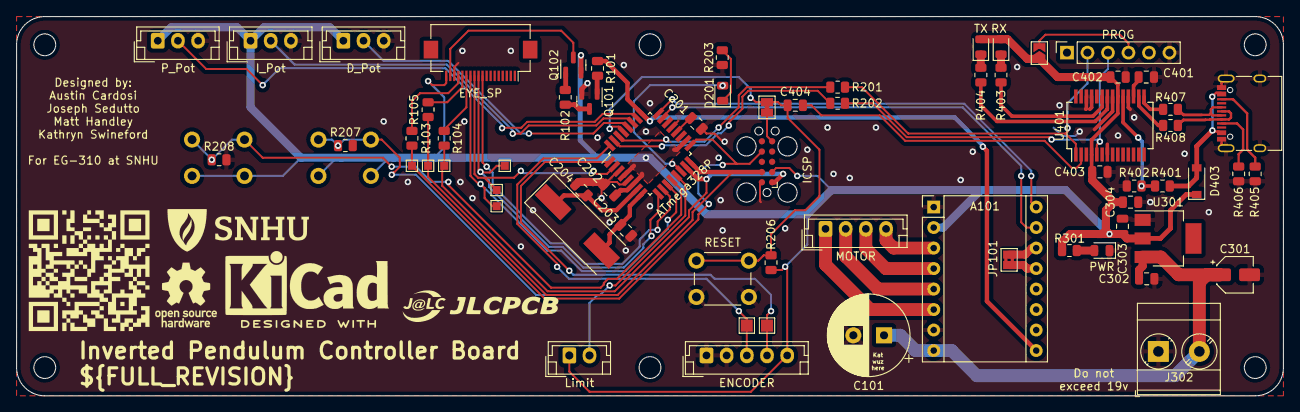
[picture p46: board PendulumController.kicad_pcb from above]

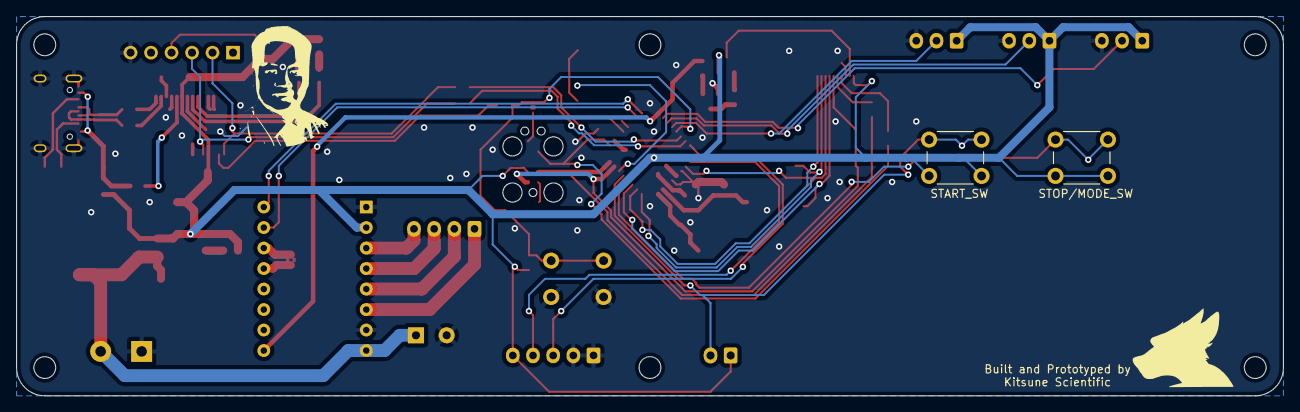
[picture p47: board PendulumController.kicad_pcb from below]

Board: 2 copper layers, 157.0 x 47.0 mm, 78 parts (2 on the bottom side), 60 nets.

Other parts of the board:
QRCODE: LOGO; custom_silkscreen
SNHU_NEW***: LOGO; SNHU_NEW

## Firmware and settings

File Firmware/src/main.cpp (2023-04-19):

/**
 * @file main.cpp
 * @author Joe
 * @brief Source code for EG-310 Pendulum demonstrator
 */

// AVR/System
#include <Arduino.h>
#include <Encoder.h>

// Our libs
#include "display.h"
#include "calibrate.h"

// Pindefs and misc
#include <boardPins.h>

// Instantiate Objects
Display tft = Display(TFT_CS, TFT_DC, TFT_RST);
Encoder encoder(ENC_A, ENC_B);

void setup(void)
{
    // Configure serial
    Serial.begin(115200);
    Serial.println(REV);

    // Begin our display
    tft.begin();
    tft.loading(0); // Update the loading bar

    // Inputs and Outputs
    pinMode(STAT_LED, OUTPUT);
    pinMode(ENABLE, OUTPUT);
    pinMode(DIR, OUTPUT);
    pinMode(STEP, OUTPUT);
    pinMode(PPIN, INPUT);
    pinMode(IPIN, INPUT);
    pinMode(DPIN, INPUT);

    digitalWrite(ENABLE, HIGH);
    digitalWrite(STAT_LED, HIGH);
    digitalWrite(DIR, HIGH);

    // Done loading
    tft.loading(100);

    // calibrate(encoder);
    Serial.println(F("Done. Encoder is now at "));
    Serial.println(encoder.read());
}

const int MAX_SPEED = 900;
int setpoint = -100;
int pos = 0;
int err = 0;
int divisor = 0;

// For harmonic oscilation
int freq = 1300; // 1/hz
int encMax = 100;
int lastMax = 0;

void updateMotor()
{
    if (abs(err) < 800)
    {
        int delay = map(abs(setpoint), 0, 100, 20000, MAX_SPEED);
        if (setpoint > 0)
        {
            digitalWrite(DIR, HIGH);
            pos++;
        }
        else
        {
            digitalWrite(DIR, LOW);
            pos--;
        }

        digitalWrite(STEP, HIGH);
        delayMicroseconds(350);
        digitalWrite(STEP, LOW);
        delayMicroseconds(delay);
    }
}

bool myDir = true;

bool spinUpDone = false;
void spinUp()
{
    if (abs(encoder.read()) < 30 && millis() - lastMax > 400)
    {
        freq = freq * -1;
        Serial.println("Hit apex!");
        lastMax = millis();
        encMax = 0;
    }
    setpoint = freq;

    if (abs(encoder.read()) > 2000)
    {
        spinUpDone = true;
        Serial.println("Spinup done.");
    }
}

void loop()
{
    // Plot table
    // tft.plot(encoder.read() / 100);

    // Draw screen
    // Serial.println("Drawing New Issues");
    // tft.displayIssues();

    // Blink
    // digitalWrite(STAT_LED, HIGH);
    // delay(100);
    // digitalWrite(STAT_LED, LOW);
    // delay(100);

    // -  (pos * 0.01)
    if (spinUpDone)
    {
        err = encoder.read() - (COUNTS_PER_ROTATION / 2) + (-pos / 350);

        // Primitive I
        if (abs(err) < 20)
        {
            err = err * 1.3;
        }

        setpoint = constrain((err * 0.3) * 10, -101, 101);
        setpoint = -setpoint;

        Serial.println(err);
    }
    else
    {
        spinUp();
    }

    divisor++;
    if (divisor >= 10)
    {
        divisor = 0;
        tft.plot(err);
    }

    updateMotor();
}

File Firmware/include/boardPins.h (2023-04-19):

#include <Arduino.h>

#ifndef _BOARD_PINS_H
#define _BOARD_PINS_H

// LEDs
#define STAT_LED 10 // PB2

// Power Control
#define ENABLE A2 // PC2

// Motor
// #define STEP A0 // PC0
// #define DIR A1  // PC1
#define STEP 7  // PC0
#define DIR 8   // PC1
#define ENC_A 2 // PD2
#define ENC_B 3 // PD3

// Buttons and Inputs
#define PPIN A3     // PC3
#define IPIN A4     // Also SDA, PC4
#define DPIN A5     // Also SCL, PC5
#define STOP_MODE 8 // PB0
#define START 9     // PB1

// TFT Display
#define TFT_RST 4 // PD4
#define TFT_CS 5  // PD5
#define SD_CS 6   // PD6
#define TFT_DC 9  // PD7

#endif

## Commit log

2023-01-03 Boilerplate project
    [PendulumController.kicad_pcb, PendulumController.kicad_sch, mcu.kicad_sch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]
2023-01-03 Cleanup board layout, cleanup firmware and go to bed, this is a sturdy place to start a new project!
    [PendulumController.kicad_pcb, PendulumController.kicad_sch, mcu.kicad_sch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]
2023-01-03 Configure kibot config
    [power.kicad_sch]
2023-01-03 Add power flags
    [PendulumController.kicad_sch]
2023-01-03 Spitballin' with Matt
    [3dSketch.blend, NEMA17.step]
2023-01-03 Cleanup readme and fix ERC
    [PendulumController.kicad_sch, power.kicad_sch]
2023-01-03 Add notes for timer code
2023-01-03 Add TFT connector
    [PendulumController.kicad_pcb, PendulumController.kicad_sch, mcu.kicad_sch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]
2023-01-04 Add sample presentation in LaTeX
2023-01-04 Improve readme and clean notes
    [3dSketch.blend]
2023-01-09 ConOps Draft (#2)
    Submitting as soon as folder is available
    [Pendulum Team Hours Worked.xlsx]
2023-01-09 Docs and Cosmetic (#4)
    Great!
    [Badge.blend]
2023-01-12 Merge ProjectLibre
    Merging this, future branches will reference main.
    [3dSketch.blend, TempCam.FCStd]
2023-01-29 Feat/pdp draft #1 (#8)
    Hey this is great! PDP draft went well, I'm merging this in favor of a new branch.
    [Pendulum Team Hours Worked.xlsx, Pendulum328BOM.csv]
2023-02-16 V1 Board (#3)
    [PendulumController.kicad_pcb, PendulumController.kicad_sch, mcu.kicad_sch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]
2023-02-16 fixup! V1 Board (#3)
2023-02-22 CDR Prep (#11)
    This is good to go thank you @AustinC63
    [3764N101_High-Strength Gt Timing Belt Pulley.ipt, 91290A169_Alloy Steel Socket Head Screw.ipt, A4988.iam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]
2023-04-10 Inital Frame and motor assembly (#13)
    [Electronics.step, ElectronicsAndBezel.FCStd, Frame.FCStd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]
2023-04-10 Firmware (#15)
    Merged for PRR
    [PendulumController.kicad_pcb, PendulumController.kicad_sch, mcu.kicad_sch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]
2023-04-19 Final Presentation (#18)
    [NewMotorAdapter.FCStd, Pendulum Project Verification Matrix.xlsx]
